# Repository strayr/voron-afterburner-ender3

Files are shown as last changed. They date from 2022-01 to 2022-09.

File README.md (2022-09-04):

# Afterburner Carriage for Ender 3 v2

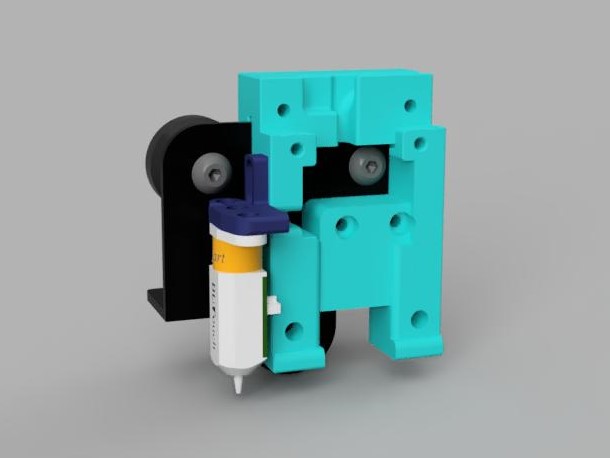
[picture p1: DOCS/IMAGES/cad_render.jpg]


This is my effort to get an afterburner/stealthburner on my ender 3 v2, and reuse the creality hotend. Some of the other models modify the casing of the clockwork and i'd much rather have the full modularity the afterburner provides, so i can slot in different extruders and toolheads or even a dual/triple bowden adapter from the switchwire multi extrusion effort. This isn't really intended as an endpoint but a step between and Ender3 and building a Voron.

I maintain a [creality toolhead for stealthburner](https://github.com/strayr/stealthburner_creality_edition) separately.
## User story

This was built as a way to try out afterburner before going all in on a Voron. Vorons have a pit of a reputation for being ABS machines, and as most models are designed to be enclosed they are **very** good at printing abs. The default 4020 fan afterburner is allegedly a bit feeble for printing ABS fast.

I had been using a [Hydra](https://www.thingiverse.com/thing:4062242) toolhead with dual 5015s on my ender 3 and had tried all the prusa toolheads on what started out as a self-sourced MK2 clone. The Hydra is **very** good but lacks good probe support, keeping the probe so far from the nozzle that it is not possible to probe a large stripe of the bed. The prusa toolheads weren't as good at overhangs and are very difficult to work on. The [afterBEARner](https://www.prusaprinters.org/prints/54545-afterbearner-the-prusa-bear-afterburner) carriage is worth investigting for use on linear rod printers and i have one on my mk2 frame.

My starting point for part cooling was [Greg191134's 5015 mod](https://github.com/Greg191134/Voron/tree/master/Afterburner%20Optimisation/5015%20fan%20mod) with the standard afterburner duct/hotend mount which worked ok, but I quickly printed [The Warbird](https://github.com/Greg191134/Voron/tree/master/Afterburner%20Optimisation/The%20Warbird) which does PLA a lot better, but I had some issues with the duct deforming. 

[Badnoob](https://github.com/VoronDesign/VoronUsers/tree/master/printer_mods/Badnoob/AB-BN)'s fan duct and toolhead was the part that really made this viable for me, and this was when i started ordering parts and [Stealthburner Beta](https://github.com/VoronDesign/Voron-Afterburner/tree/sb-beta) is incrediby impressive. I will update the carriage to support clockwork 2.

 ## Future

This is considered complete, I no longer have an ender 3, it's now a VS.373. Stealthburner toolhead has it's own repository now and will continue to be supported.
## Changes

- Remove stealthburner, link to new repo.

- 5 added a stealthburner toolhead mount that fits Creality hotends. 

- 4 made a clockwork 2 comaptible version.

- 3 Shared my AB-BN toolhead mod for creality hotends. It only works with the AB-BN-30 fan shroud, not afterburner or stealthburner. It's better with a v6 type nozzle and slightly longer screws on the hotend, and i'm using a bimetallic heatbreak. I don't recommend anyone go out and buy a slice heatbreak, if you want an upgrade buy a voron supported hotend. I get really nice results with my v6s, but I'm using this on one printer as I;m a cheapskate. May have jams if you use a 12v or silent fan. Works great with stock 24v creality fan. 
- 2 Made a mount that sits on the right hand side of the carriage close to the stock x position. Hopefully the nozzle will require less X offset and can probe more of the bed due to extra travel available of the carriage beyond the right side of the bed.
- 1 Initial commit

## Compatibility

This is known to fit a late 2020 production Ender v2, it might not fit older pros and vanilla ender 3s.

The afterburner carriage fits clockwork 1, AB-BN-30 and the stealthburner fan shroudand toolhead. It doesn not fit clockwork 2. ~~A clockwork 2 compatible carriage will happen shortly.~~ ERCF modified clockwork should fit. A modified version that should fit Clockwork 2 is availabe in the CW2 folder.

The Omron inductive probe does not fit, and is not compatible with the creality v-roller carriage. I use this with a BL-Touch. If you really want to use an omron style inductive probe you will likely need a linear rail setup, i suggest you consider converting your ender 3 into a switchwire.

Some alterations to your firmware configuration may be required. I will not provide support for Marlin configs, you're on you own there. I'm a klipper user and highly recommend it if you change your hardware often as configuration is all done in text files and you just restart the printer after making changes.

## Duct/mount for creality hotend

I have a fancy and expensive bimetallic heatbreak for the creality hotend and wanted to continue using it. It cost as much as buying an entire E3D V6 which has a better thermistors and heater, and works just as well. I get best performance out of a V6 with a titanium heatbreak, although I think i'm using a clone heatsink. I have a clone copper heater block on one of my V6s, i'm not sure it makes any difference. 

I'm using E3D nozzles with my creality hotend which required some longer screws between the heater block and heatsink. These should be stainless steel if possible. Screw the nozzle almost all the way into the heater block, with maybe 1mm between the hex flange of the nozzle and heater block and then screw the heatbreak in, it will sit prouder than usual but it works. I have not tested this toolhead with mk8/creality style nozzles, but the cad suggests it will fit. The overall lenght of the hotend doesn't change appreciably when using E3D style nozzles, they are close to the same lenght overall as the creality ones but have a longer threaded section and shorter length after the flange. They provide slightly better filament heating and much better ironing performance.

Do not use a "silent" fan with the creality hotend, it needs the flow of a 24v high flow cooling fan, the stock creality one is ok, you don't need to buy an expensive one, but if you have a noctua 4010 or a cheap silent fan it will probably cause jams, certainly it did for me.

## Contents
### RightHandMount
I reworked my original to mount near where the original hotend mounts, it should make for easier use without custom firmware and allows more ofthe bed to be probed. You may need to turn around the bolt on the lower v-roller so the head faces the gantry, this will allow more X travel.

[RightHandMount](https://github.com/strayr/voron-afterburner-ender3/tree/main/RightHandMount)

Cad Model of carriage

### OriginalMount

This is my [original](https://github.com/strayr/voron-afterburner-ender3/tree/main/OriginalMount) version, centered on the carriage plate, it's more stable but if you use a probe it can't reach as much of the bed. It works well but I prefer the right hand mount. It may require custom firmware.

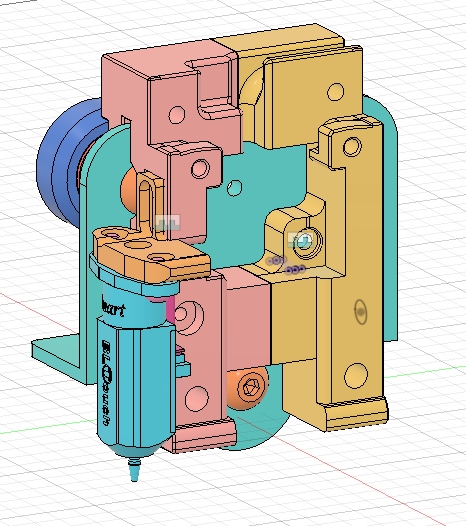
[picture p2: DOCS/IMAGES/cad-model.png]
Cad Model of carriage


### AB-BN toolhead

My first attempt at reusing my creality hotend

### Strealthburner toolhead

UMy second attempt at reuse of a creality hotend. The stock ptfe lined is not really recommended, but if you have an all metal heatbreak it can work quite well. The E3D Cyclops heatbreak is cheap and fits. I use a Slice Copperhead heatbreak and continue to adapt toolheads for it becasue sunk cost. Just get a v6/revo/dragon/whatever voron supports if you haven't already spent money here.

I strongly recommend longer stainless steel screws on the heather block and a V6/reprap style nozzle here, they have a longer thread and stick out less from the heater block, and unscrewing the heat break a little to accommodate these can move the heater block further away form the printed parts of the toolhead.

## Printing

Use the settings at recommended by Voron

>The Voron Team has provided the following print guidelines for you to follow in order to have the best chance at success with your parts There are often questions about substituting materials or changing printing standards, but we recommend you follow these.
### PRINTING PROCESS
Fused Deposition Modeling (FDM)
### MATERIAL
ABS _I have tried this in PET-G on an unenclosed printer, but you will need to print the parts that get close to the heater block in ABS or ASA. Clockwork works in PET-G, and the yellow parts in my photo are PLA, and hasn't broken yet._
### LAYER HEIGHT
Recommended: 0.2mm
### EXTRUSION WIDTH
Recommended: Forced 0.4mm _this appears to apply to cura and assumes rectangular extrusion cross section, PrusaSlicer/SuperSlicer assumes round ends, and 0.45mm extrusion width results in ~0.40mm between extrusions._
### INFILL TYPE
Grid, Gyroid, Honeycomb, Triangle or Cubic
### INFILL PERCENTAGE
Recommended: 40%
### WALL COUNT
Recommended: 4
### SOLID TOP/BOTTOM LAYERS
Recommended: 5
## Disclaimer

This is provided entirely without warranty and it is entrely up to the user do assess the suitability of this for the intended use.

## License

This is provided under a [GNU GPL 3.0 licence](./LICENSE). 

Do not publish under another license. You must provide your CAD source for any changes. STL is not source. We have such an amazing array of printers available becasue of the open source nature of the [RepRap](https://reprap.org) project and [OpenHardware](https://www.oshwa.org). Both the [Creality Ender 3](https://github.com/Creality3DPrinting/Ender-3) and the entire [Voron project](https://github.com/VoronDesign) are open source.

Give Back. 

## Contact

Please raise an issue on my github if you have specific issues. I cannot provide support for all your problems, but if my designs don't work for you I want to know and may attempt to improve them. This is entirely a hobby and motivated out of self interest.

## See Also
  - [Voron Afterburner](https://github.com/VoronDesign/Voron-Afterburner) this is the original toolhead this carriage mounts, you will need to print this to get a useable toolhead. Read thir documantation carefully for what parts to print.
  - [Stealthburner Beta](https://github.com/VoronDesign/Voron-Afterburner/tree/sb-beta) this is the original toolhead this carriage mounts, you will need to print this to get a useable toolhead. Read thir documantation carefully for what parts to print.
  - [AB-BN](https://github.com/VoronDesign/VoronUsers/tree/master/printer_mods/Badnoob/AB-BN) user mod fan duct and toolhead compatible with afterburner/clockwork, the basis for StealthBurner.
  - [Greg191134](https://github.com/Greg191134/Voron/tree/master/Afterburner%20Optimisation) Alternate 5015 fan housing and Warbird Duct
  - [Enraged Rabbit](https://github.com/EtteGit/EnragedRabbitProject/blob/main/README.md) multimaterial project

## Gallery
Afterburner duct, clockwork extruder and Greg191134's 5015 fan mod

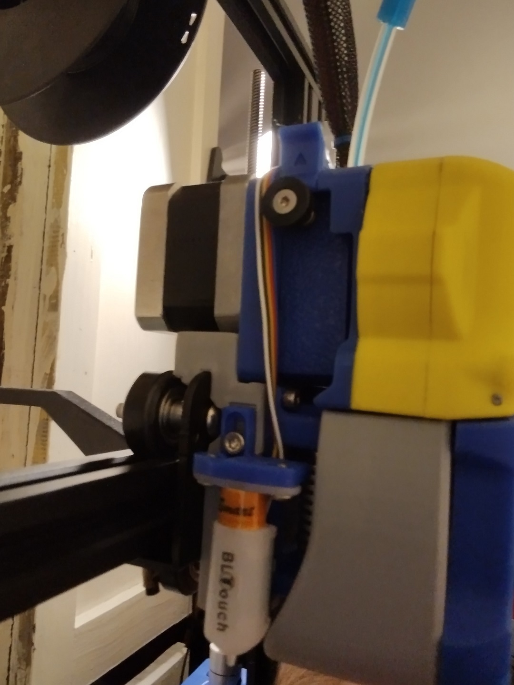
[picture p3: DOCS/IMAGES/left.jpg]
Left side of carriage with afterburner mounted


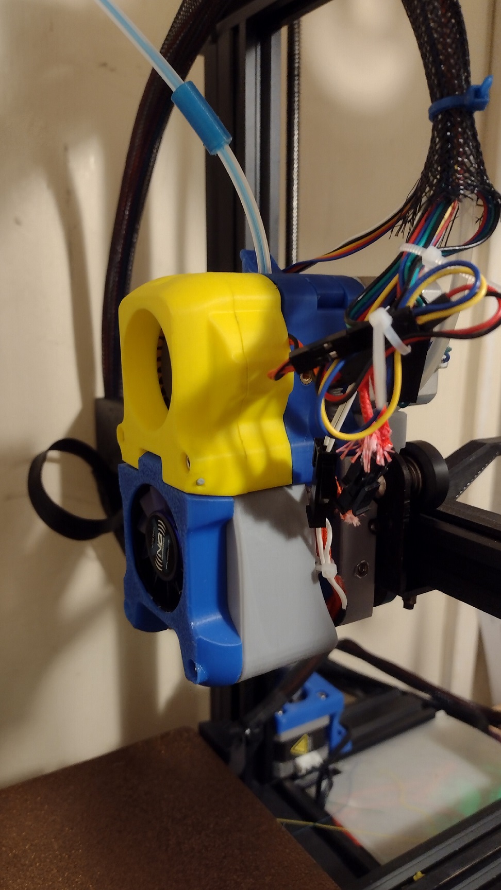
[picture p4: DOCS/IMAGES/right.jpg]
Right side of carriage with afterburner mounted


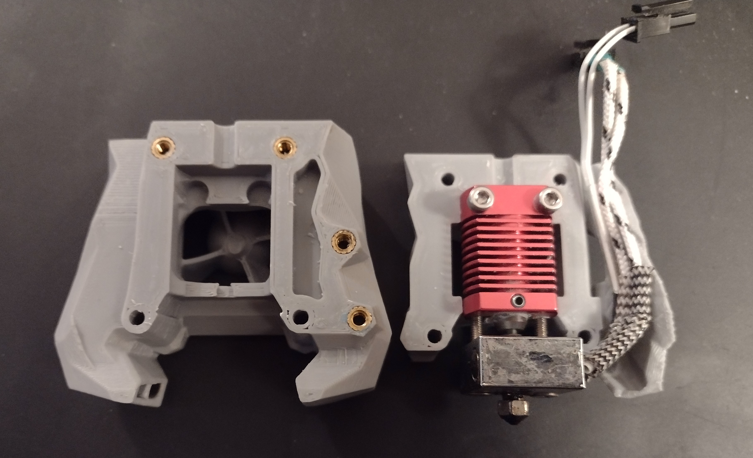
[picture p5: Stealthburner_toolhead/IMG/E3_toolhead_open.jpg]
E3 hotend in stealthburner toolhead


Stealthburner (left) and AB-BN-30 (right) with Ziro PLA

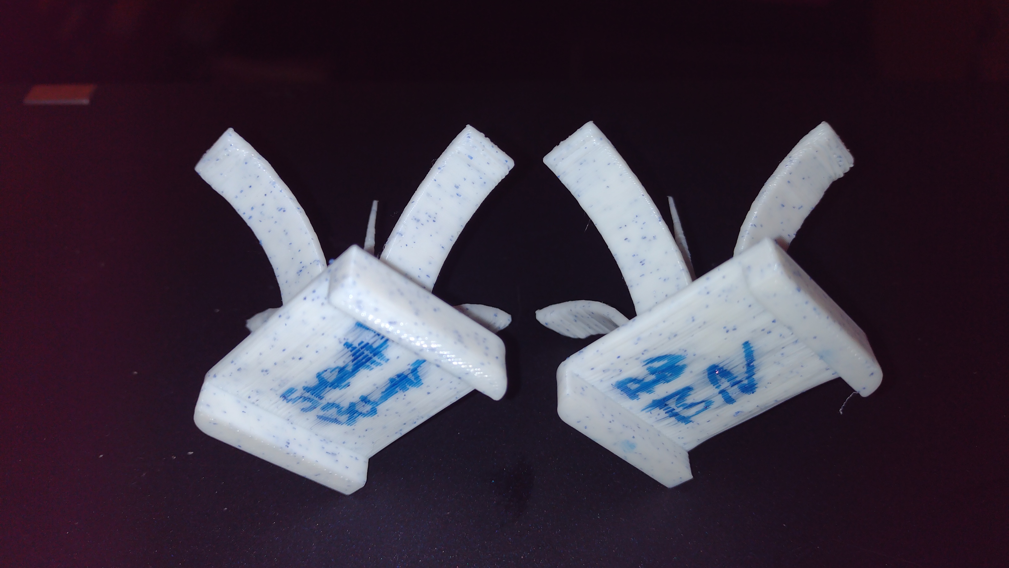
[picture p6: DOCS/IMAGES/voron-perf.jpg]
Badnoob and Stealthburner performance


Prusa (left) and Hydra (right) with 3dTomorrow PLA

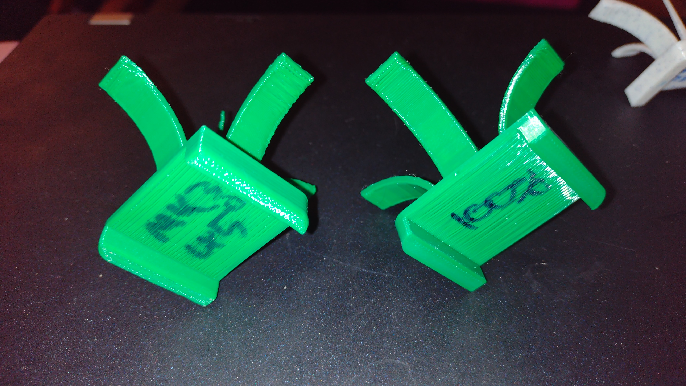
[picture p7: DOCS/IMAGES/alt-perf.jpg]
Prusa and Hydra performance


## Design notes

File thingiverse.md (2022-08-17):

Summary

This was based on my remix of lessananon1's afterburner bracket to fit an Ender 3 V2 plate with a BLTouch.

# Ender 3 v2 Hydra Mount

Part removed from thingiverse due to their anti-adblocker system requiring me to turn off all of Firefox's tracking protection. This is intrusive and I don't like it. I don't run an adblocker, but I like my privacy. Part is available at https://github.com/strayr/voron-afterburner-ender3

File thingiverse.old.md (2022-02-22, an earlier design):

Summary

Just a quick remix of lessananon1's afterburner bracket to fit an Ender 3 V2 plate with a BLTouch.

It only fits the V2. There'sa big bolt in the way interfereing with the voron style inductive probe, so I added a brace where that should go for a bit more rigidity.

The rest of the afterburner is on the voron github https://github.com/VoronDesign/Voron-Afterburner

I'm using this 5015 fan mod https://github.com/Greg191134/Voron/tree/master/Afterburner%20Optimisation/5015%20fan%20mod

Best printed in ABS with 4 perimeters, 5 top and bottom layers and 40% infil as per voron specs. eSun ABS+ works well if you don't have an enclosue and the draft shiled option in prusaSlicer/superslicer really helps.

Even using a cardboard box as an enclosure helps, i have an ABS prusa in a lack box and am using it to build a voron, but everyththing has afterburners as the part interchangability is really helpful, as is breing able to use the same filament settings on every printer.

You will need to print the fan duct in ABS or ASA and the clockwork extruder needs to be PETG if unenclosed or ABS if enclosed. Don't consider this if you can only print PLA.

This is GNU GPL V3, thingiverse doesn't do licencing properly. lessananon1's part uses the voron source so must be GPL V3, I'm including attribution as a courtesy.

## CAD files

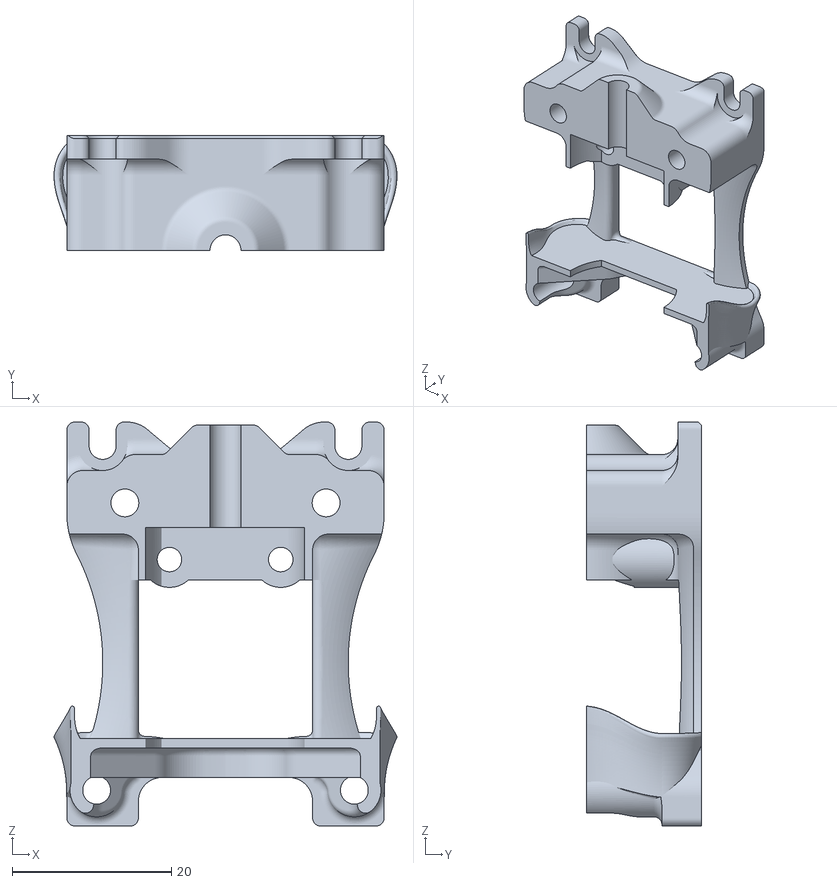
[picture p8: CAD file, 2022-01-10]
AA-BN-30_toolhead/toolhead_back.stl
43.1 x 14.5 x 50.8

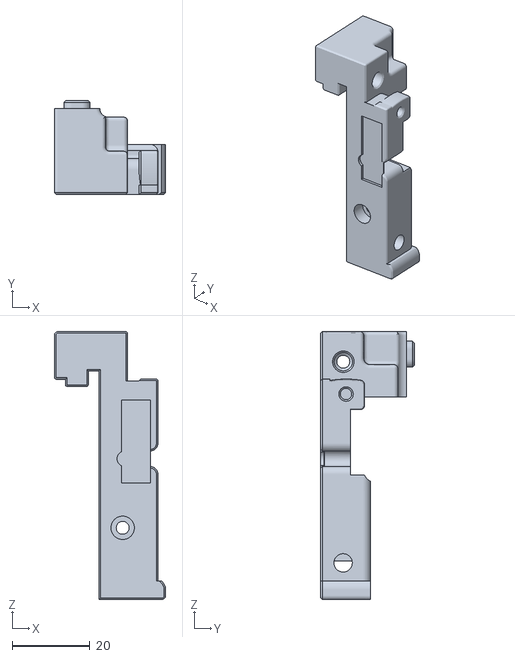
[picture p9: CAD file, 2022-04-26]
CW2/STL/carriage_left_cw2.stl
28.6 x 24.0 x 68.8

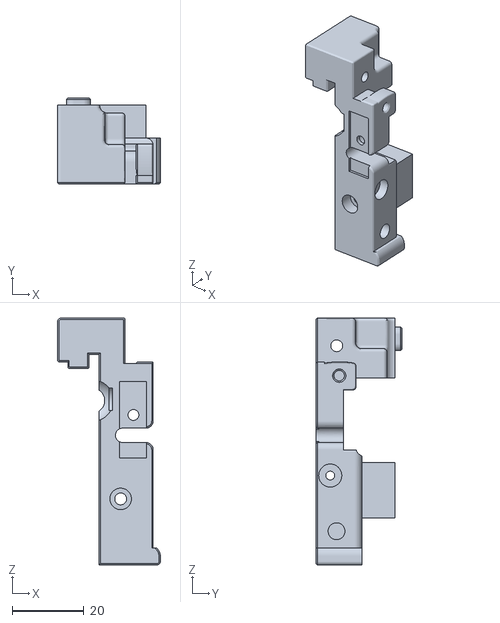
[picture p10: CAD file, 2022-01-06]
OriginalMount/STL/X_Carriage_Frame-35X_Carriage_Frame_X_Carriage.stl
28.6 x 24.0 x 68.8

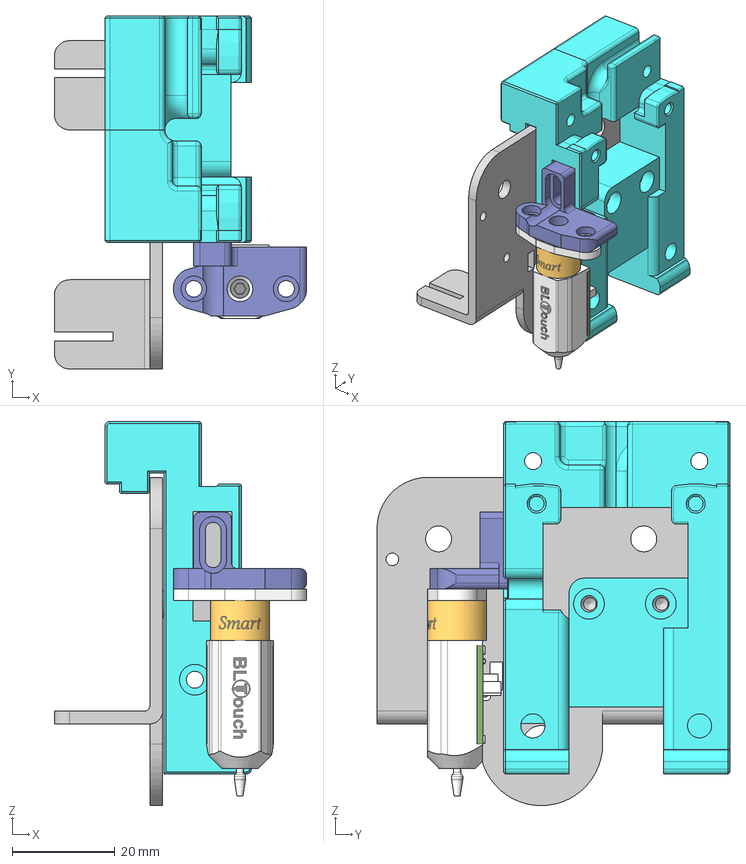
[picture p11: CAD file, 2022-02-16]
RightHandMount/CAD/Afterburner_Ender3v2 v2 v7.step
49.2 x 68.8 x 74.9 mm
X Carriage Frame-35^X Carriage Frame_X Carriage
X Carriage Frame-36^X Carriage Frame_X Carriage
BLTOUCH_V3-1
BL_Toch Mount
Bracket_Main_hotend-X axis

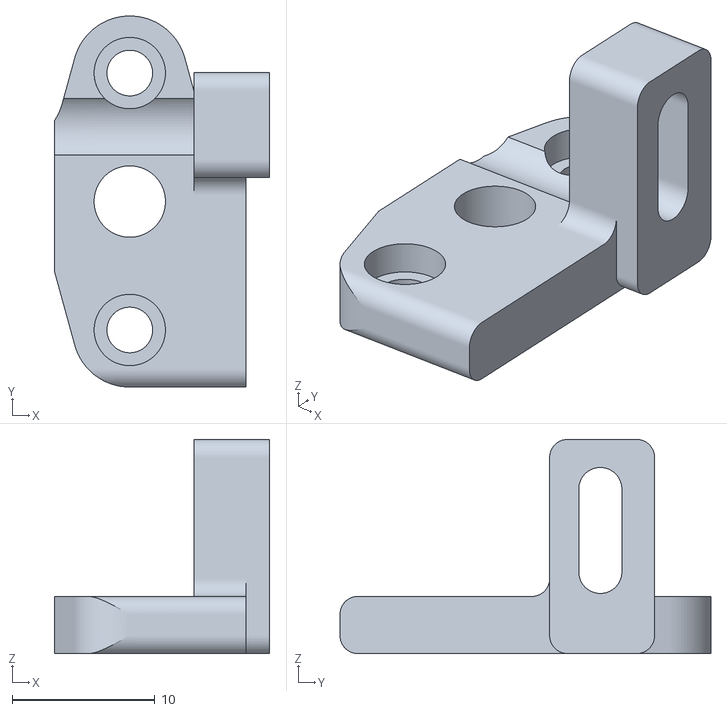
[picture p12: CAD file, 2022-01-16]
RightHandMount/STL/probe_mount.stl
15.1 x 26.0 x 15.0

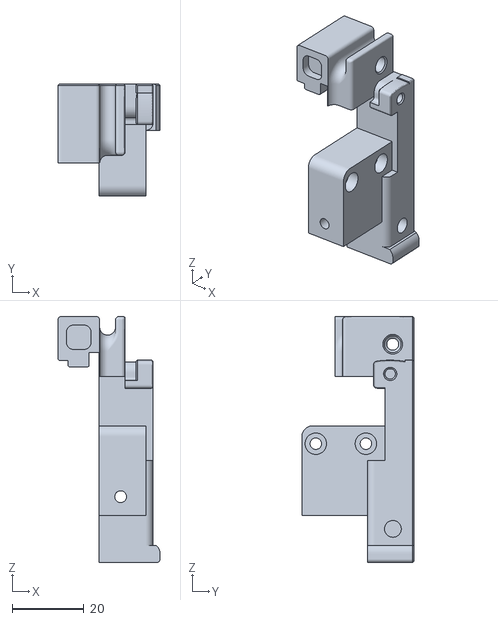
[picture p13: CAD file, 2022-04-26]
CW2/STL/carriage_right_cw2.stl
28.6 x 31.4 x 68.8

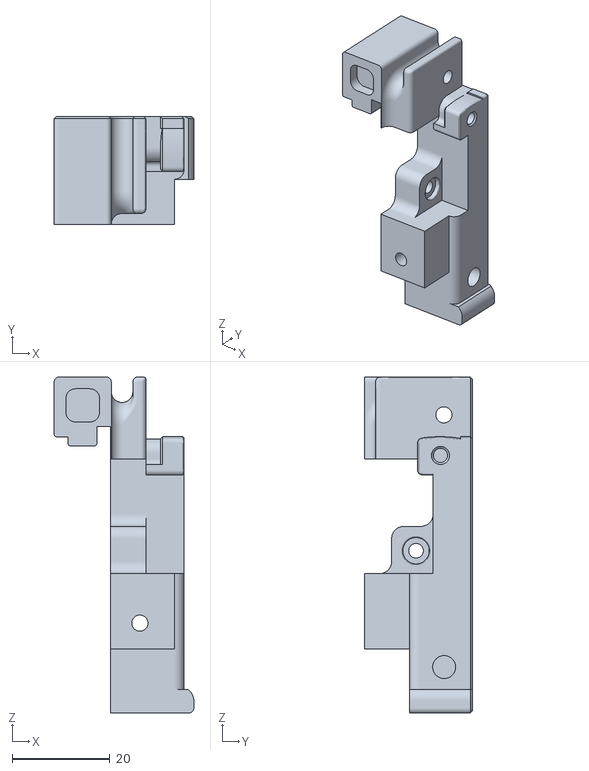
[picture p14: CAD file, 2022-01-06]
OriginalMount/STL/X_Carriage_Frame-36X_Carriage_Frame_X_Carriage.stl
28.6 x 22.0 x 68.8

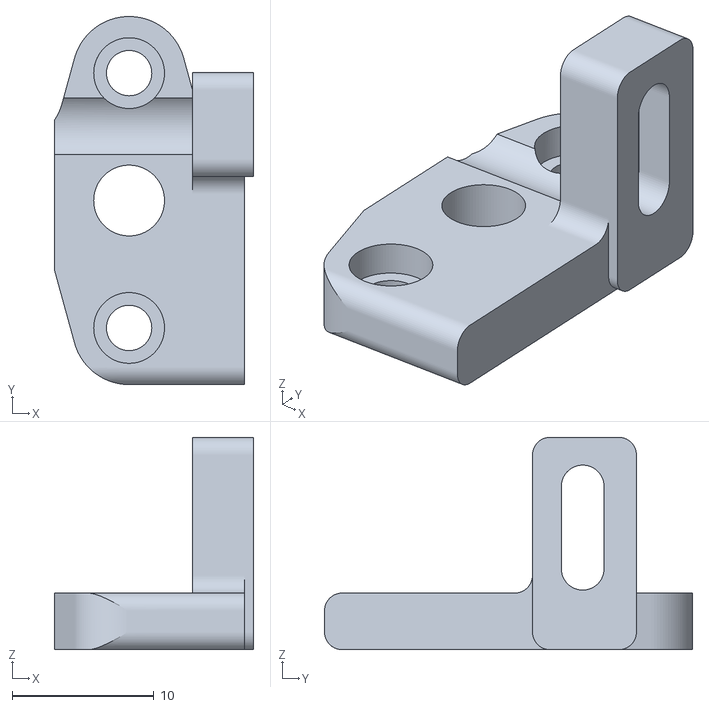
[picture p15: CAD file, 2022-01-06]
OriginalMount/STL/BL_Touch_Mount.stl
14.1 x 26.0 x 15.0

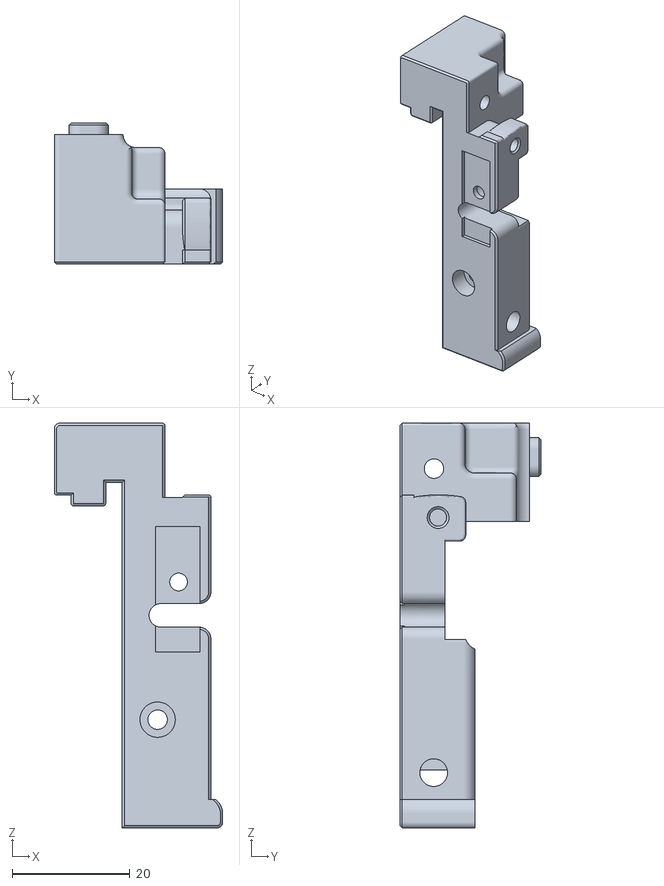
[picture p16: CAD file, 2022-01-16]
RightHandMount/STL/carriage_left.stl
28.6 x 24.0 x 68.8

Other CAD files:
RightHandMount/STL/carriage_right.stl

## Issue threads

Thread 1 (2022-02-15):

Export CAD to other formats?

frap129, 2022-02-15:
Hey, I'm looking to make some modifications to make sure that this fits an original Ender 3 carriage plate without having to print the mount out and physically modify it. I don't have fusion installed (and would prefer not to have to install it just to convert one file), so could you export the right hand mount in a different format? STP/STEP, OCA, or IGES would be fine, just need something I can open in FreeCAD. Thanks!

Edit: I used the STLs and it looks like it'll work, but I would still appreciate a CAD file I can use so I can add correct mounts for clockwork 2

strayr, 2022-02-16:
I have taken this on board and have started exporting step with new changes, I'll see if I can drop you some STEP for these. I think I'm going to drop a clockwork2 carriage here as well the interface seems pretty stable and people keep asking.

strayr, 2022-02-16:
#6a41a22 should be step for the right hand carriage

frap129, 2022-02-16:
Thanks! I appreciate it. Not sure what hotend you use, but here's an untested hotend mount for the microswiss all metal CR-10/Ender (Should fit all mk8 hotends) as thanks [https://www.thingiverse.com/thing:5249466](https://www.thingiverse.com/thing:5249466)

strayr, 2022-02-16:
I've got some V6 hotends and a Creality heatsink with a slice engineering
copperhead C-E heatbreak. Hence the adapted AB-BN toolhead in this repo.

Voron developers have asked NOT to distribute modified parts of
stealthburner whilst it is in beta as it pollutes the test data. They have
not made the cad available for this reason, so anything out there is
reverse engineered or made from the STLs.

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

frap129, 2022-02-16:
Whoops, didn't know that. Guess I'll delete my thing for now

strayr, 2022-02-16:
It's no big, honestly they can't stop you, it's GPL and if you asked them
for the cad (the source) they should provide as they've provided object
code, there isn't a beta exemption.

If there's demand for it and what you have is well tested, then you might
be justified putting it out there with a giant warning that it isn't an
official voron team part, don't report problems to the voron stealthburner
team, but do you trust the next remixer to listen?

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

frap129, 2022-02-17:
Yeah, I get that. I don't do much open source work anymore, but I'd want people to respect my wishes while a big project is in beta. I'll take it down and probably not re-upload it until I've tested it out for a bit

Closed 2022-02-16.

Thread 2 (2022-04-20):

Clockwork 2

tekgamerpt, 2022-04-20:
Hi... Are your files compatible with the new clockwork2? I am searching for a mount compatible with the new clockwork, with the bltouch probe and without sacrificing bed size... yours seem perfect, but im not sure that are CW2 compatible.

Cheers

strayr, 2022-04-26:
Not immediately, a small modification is required, I think i could do it in
about ten minutes though, watch this space.

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

strayr, 2022-04-26:
https://github.com/strayr/voron-afterburner-ender3/commit/5eb0040f3563403643d38c9c47ce8b5fb8d70b9d should have CW2 folder with what you need, let me know if it works for you.

tekgamerpt, 2022-04-26:
Thanks...

Closed 2022-04-26.

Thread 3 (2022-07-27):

Since there isn’t a discussion tab… THANKS!

Rick88Stang, 2022-07-27:
Printed the right mount and it works great with the clockwork 2! Printing like a beast! The only thing I’m struggling with is the offsets for the placement of the nozzle. Are you adjusting the min x & y settings in marlin? If so what have you used that works best for you. Thanks for your hard work!

strayr, 2022-07-28:
I'm using klipper, but yes you need to adjust the endstop position and bed
size in marlin.

I also move the Y extrusion forwards, just using the front screws in the
base into the rear holes in the extrusion and some shorter screws and
t-nuts for the other two.

This is fairly standard for ender3 mods, and the nozzle ends up in about
the same place in Y it is on a full switchwire conversion.

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

acesyde, 2022-11-22:
Hi @strayr thank you for this adapter, can you share your klipper configuration ?

strayr, 2022-11-22:
My macros are here https://github.com/strayr/strayr-k-macros

Snapshot configs from when various printers have been working well are here.

They're likely different in some way to anything you're running and might not be appropriate to get started.

https://github.com/strayr/sample_klipper_configs

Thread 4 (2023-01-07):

Ender 3 v2 Linear Rail Modifications

RichardTHF, 2023-01-07:
Hi there,

You said to let you know if anyone came across an issue with this, so I thought I would let you know.

I have modified my Ender 3 V2 with the Linear Rail upgrade and the "upgraded" mounting plate is actually 5mm so thicker than stock 2mm plate.

Not an issue, I just modified the STL to make it fit!

Thank you so much for making this, saved me a lot of time having to make one from scratch :)

strayr, 2023-01-07:
You should probably look at the ender 3 switchwire conversion, that's the
intended next step here.

https://github.com/SW-Conversion/mod-regisistry

I recommend looking at DaRK_dOg's version 2.

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

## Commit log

2022-01-06 Initial upload
    [BL_Touch_Mount.stl, X_Carriage_Frame-35X_Carriage_Frame_X_Carriage.stl, X_Carriage_Frame-36X_Carriage_Frame_X_Carriage.stl]
2022-01-07 change layout for multiple mounts
    [BL_Touch_Mount.stl, X_Carriage_Frame-35X_Carriage_Frame_X_Carriage.stl, X_Carriage_Frame-36X_Carriage_Frame_X_Carriage.stl]
2022-01-07 Add right hand mount
    [carriage_left.stl, carriage_right.stl]
2022-01-10 creality hotend for AB-BN-30
    [toolhead_back.stl]
2022-01-10 Create AABN-dragonbased v7.f3z
    add the cad for my toolhead
2022-01-16 Slight position tweak
    [carriage_left.stl, carriage_right.stl, probe_mount.stl]
2022-02-16 added step in response to issue #1
    [Afterburner_Ender3v2 v2 v7.step]
2022-04-26 add clockwork 2 version
    [carriage_left_cw2.stl, carriage_right_cw2.stl]
2022-08-17 initial stealthburner toolhead
    [SB C-E3 Rear CW1-nowing.stl, SB C-E3 TH Rear CW1.stl, SB C-E3 TH Rear CW2.stl]
2022-09-04 remove stealthburner toolhead
    [SB C-E3 Rear CW1-nowing.stl, SB C-E3 TH Rear CW1.stl, SB C-E3 TH Rear CW2.stl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]
